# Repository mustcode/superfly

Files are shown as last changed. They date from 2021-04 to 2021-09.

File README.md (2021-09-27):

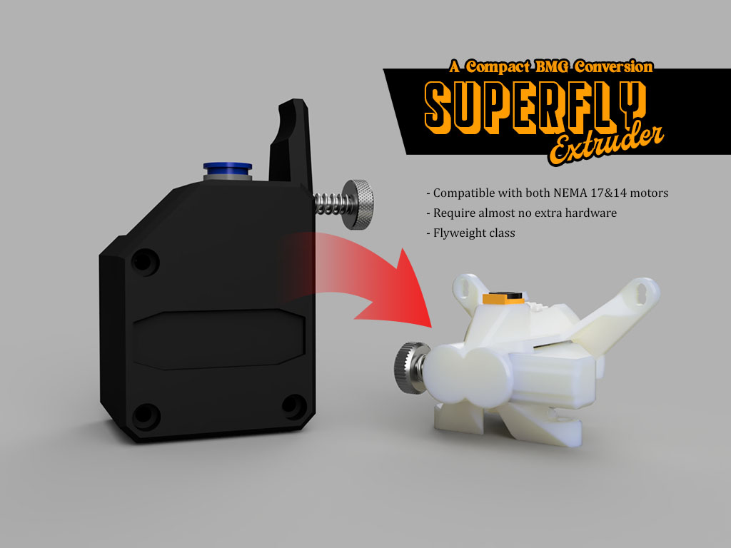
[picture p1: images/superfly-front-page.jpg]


# Superfly Extruder
### A Compact BMG Conversion

** *Update (28th Sep 2021) - A user reported an interference between the tensioner and the plastic gear when used with flexible filaments. This was an error in the design, so it is now corrected. The high-tension version is also removed as the new one should cover all use cases.*

The Superfly is a compact extruder designed to reuse the excellent dual drive gears of the beloved BMG extruder.
As with the BMG, the Superfly is a dual-drive geared extruder with a 3:1 gear ratio. It is designed with the following characteristics in mind:
- compact and lightweight
- short filament path
- balanced center of gravity
- easy to source hardware
- support both NEMA 17 and round NEMA 14 motors
- easy to print

Here are some pictures so that you can get a good idea of what the Superfly looks like:

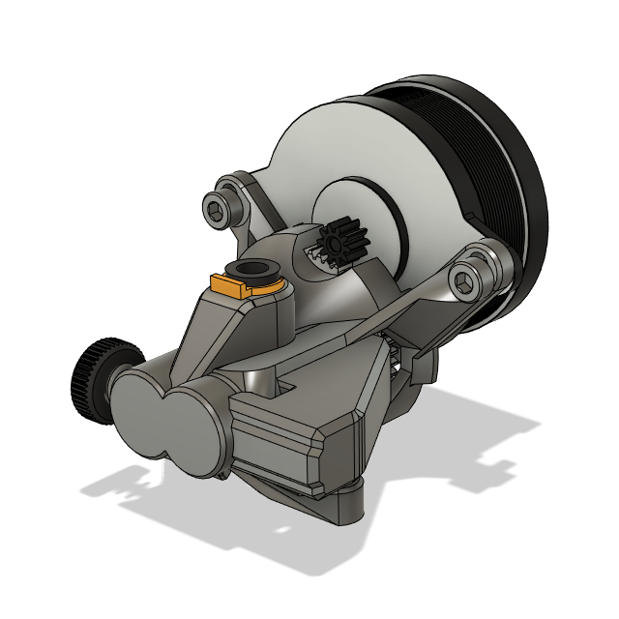
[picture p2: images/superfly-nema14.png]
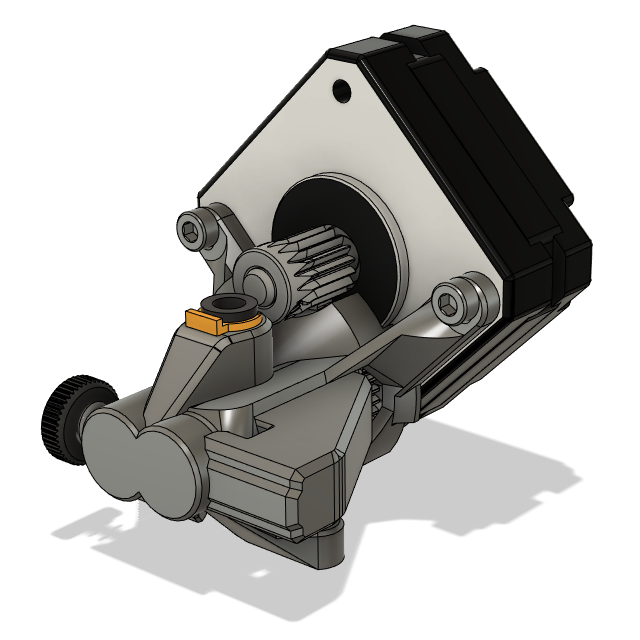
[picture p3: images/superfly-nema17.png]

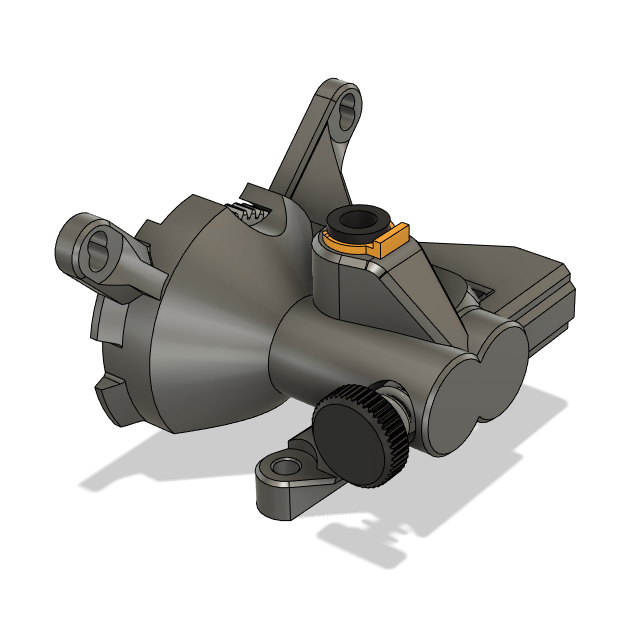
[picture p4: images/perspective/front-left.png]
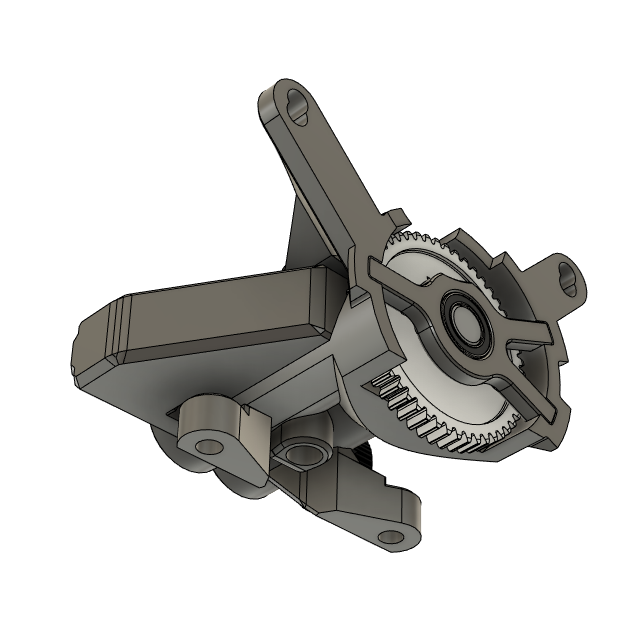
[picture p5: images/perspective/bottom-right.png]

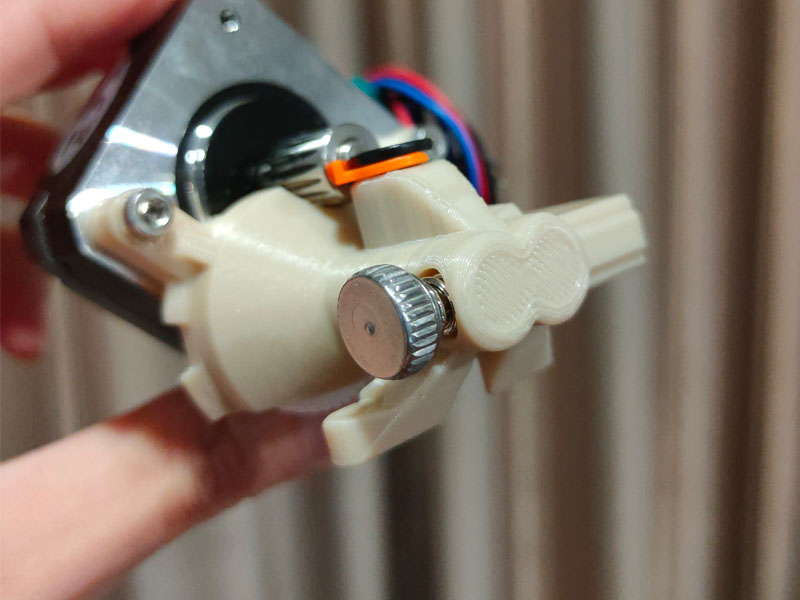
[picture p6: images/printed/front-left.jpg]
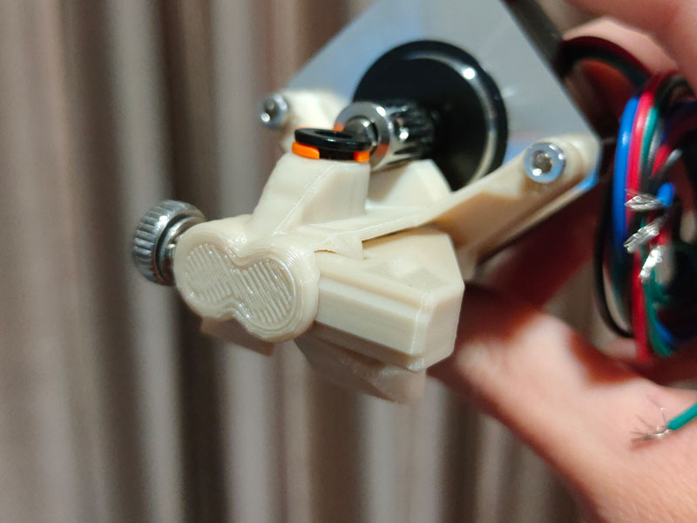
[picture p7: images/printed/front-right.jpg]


The weight of the printed parts for the Superfly comes in at less than 11 gram, a true Flyweight class!
The following shows the weight of a Superfly printed at 0.2mm layer height in PLA+ with 4 walls and plently of infill:

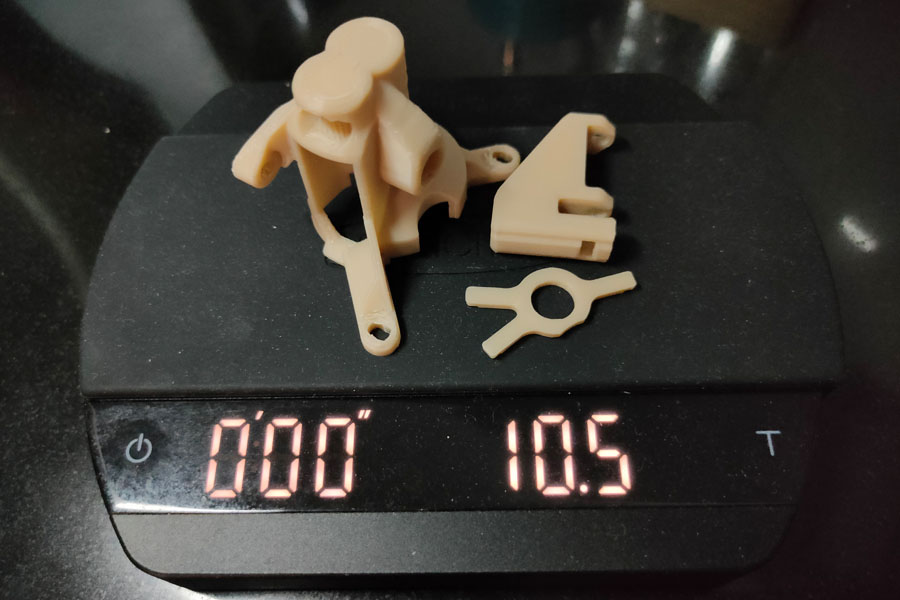
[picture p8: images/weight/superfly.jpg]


For reference, the weight of the printed parts is almost exactly the same as the Sherpa Mini with the same slicer settings:

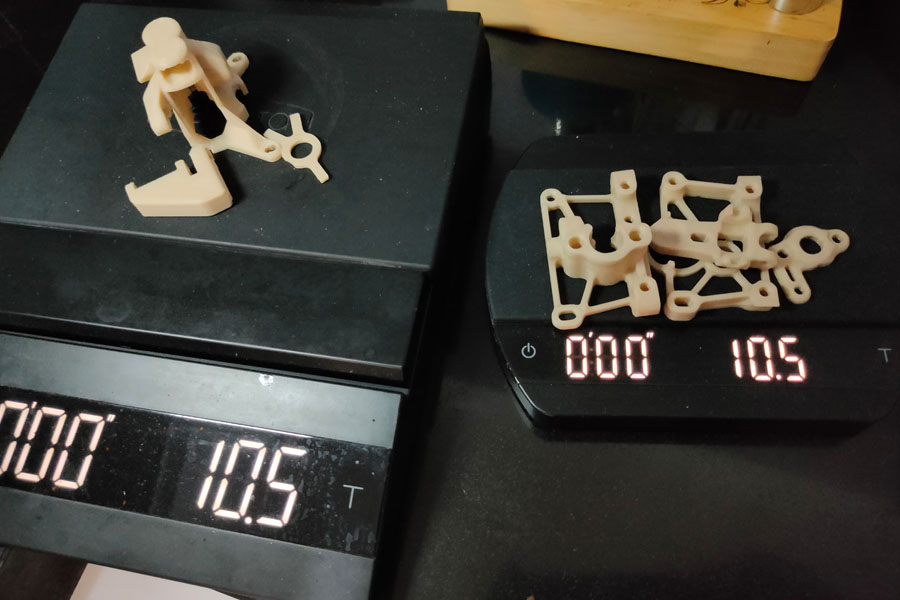
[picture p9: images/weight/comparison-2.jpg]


Fully assembled without motors, the Superfly comes in at around 30-31 gram.

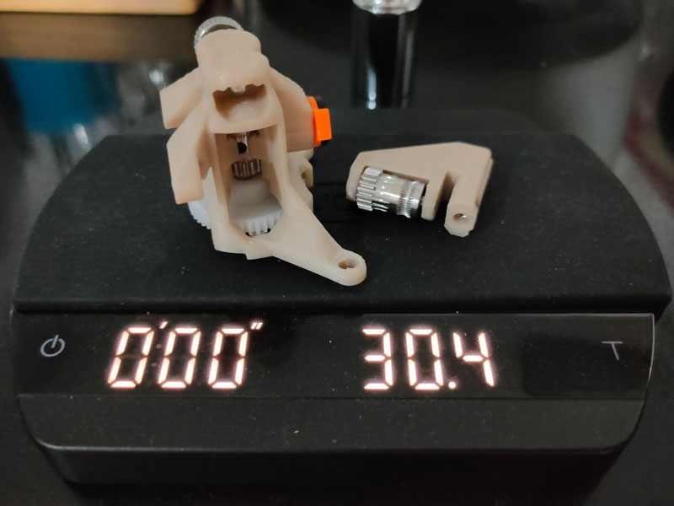
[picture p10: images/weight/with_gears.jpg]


## Parts
You will need the following parts of your BMG:
- the **drive shaft** with the large plastic gear attached
- the **drive gear**, this is the gear that is on the drive shaft
- the **idler gear**, its shaft, and the two needle bearings inside, these are the parts that were on the BMG's tension arm
- **2 x MR85 bearings** that the drive shaft runs on
- **Thumbscrew** and **spring** (the washer is optional)
- the **motor gear**, if you're planning on using a motor without a gear pre-installed

These parts can be removed without any damage to the BMG, so you can reassembled the BMG later on if you wish. If you don't already have a BMG, there are also stores that sell only these internal parts, which should be cheaper than buying a new BMG only to salvage its innards.

In addition to the BMG parts, you will also need the following hardware:
- an M3 nut for securing the thumbscrew
- 4 x M3 screws for mounting (6mm-12mm depending on your motor and mounting needs).

If you're going to be running a reverse-bowden, you'll also need:
- an embedded bowden collet (the type commonly used on a V6 heatsink)
- 4mm OD PTFE tubing

For the motor, as mentioned above, both NEMA 17 and the round NEMA 14 motors are supported. A scalable motor spacer is provided (see **The Motor Spacer** below) to help compensate for the differences in your motor's shaft length, so there's a good chance that you might already have a compatible motor on hand.

## Printed Parts
There are only 4 parts that you need to print:
- The **main housing** holds the drive gear assembly and one of the MR85 bearings.
- The **back housing** holds the other MR85 bearing and keep the drive gear assembly in the main housing.
- The **tensioner** holds the idler gear pressed to the drive gear with the tension from the spring and thumbscrew.
- The **motor spacer**, see details below:

### The Motor Spacer
The motor spacer is an optional part designed to go between the main housing and the motor to allow you to use motors with shaft longer than 15mm. Any longer than 15mm, the shaft can hit the feeding hole where the PTFE tube collet is attached:

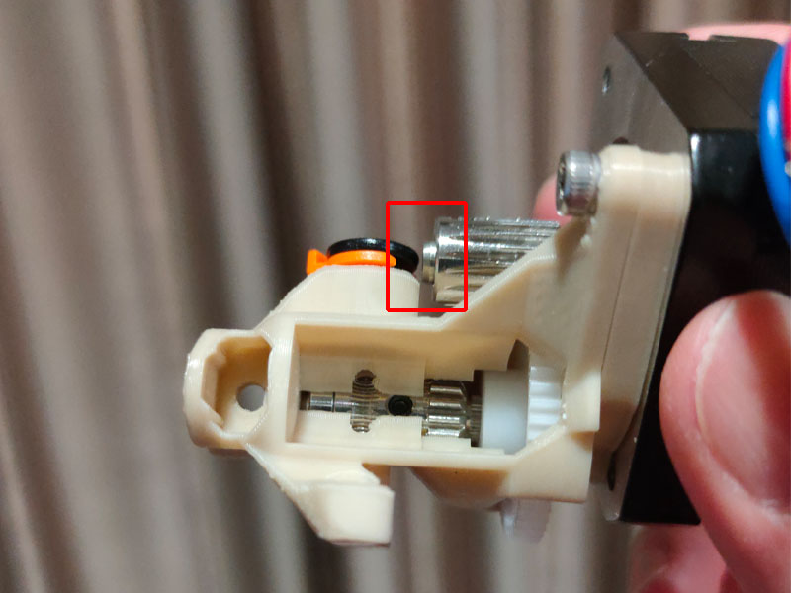
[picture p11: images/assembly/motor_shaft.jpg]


For example, if you're using a motor with 20mm shaft, you will need to scale the provided spacer to the thickness of around 4.5-5mm before printing.
Here's how the extruder looks with and without the spacer:

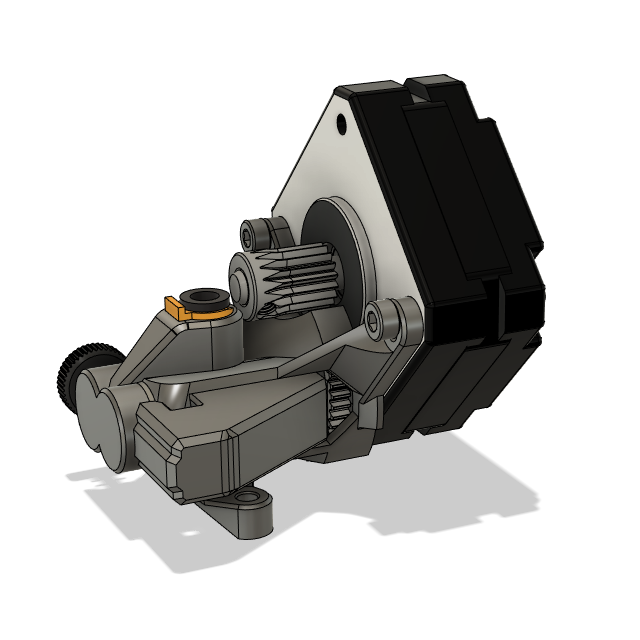
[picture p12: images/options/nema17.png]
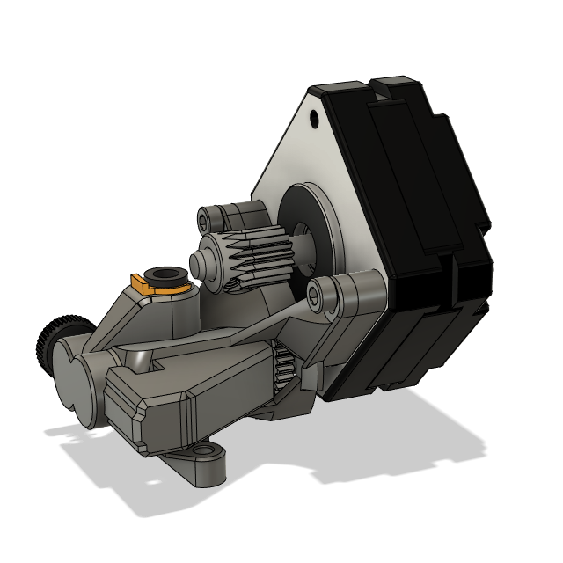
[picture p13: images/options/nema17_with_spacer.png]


Additionally, some variations of the drive shaft are known to be a bit long and may protrude beyond MR85 bearing at the back:

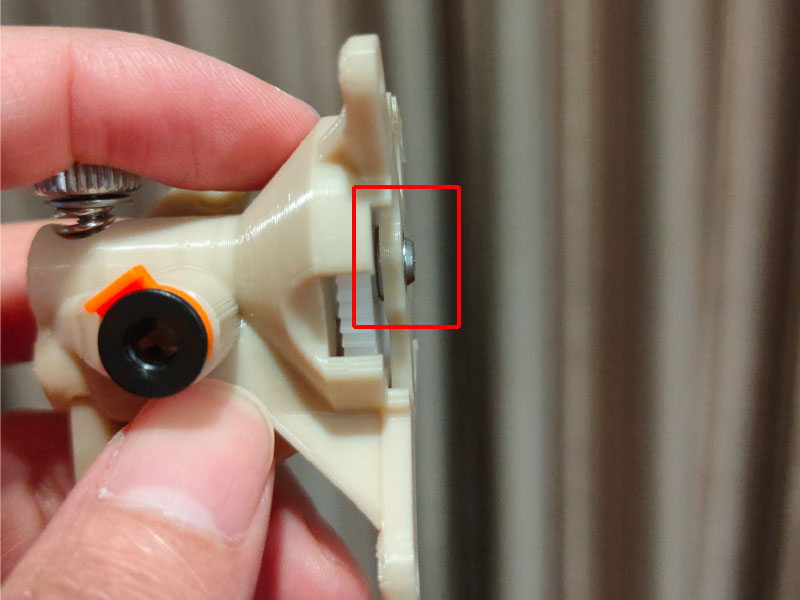
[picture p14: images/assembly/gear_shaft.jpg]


If this is the case for your drive shaft, then you will need a spacer to make sure that the shaft is not pushing against the motor's body. Finally, if you are using a NEMA 14 motor and you prefer to save weight than adding a spacer, you can grind away the protruding portion of the drive shaft, this is commonly done on other similar round NEMA 14 based extruder like the Sherpa Mini. Here's how the extruder should looks with a round NEMA 14 motor:

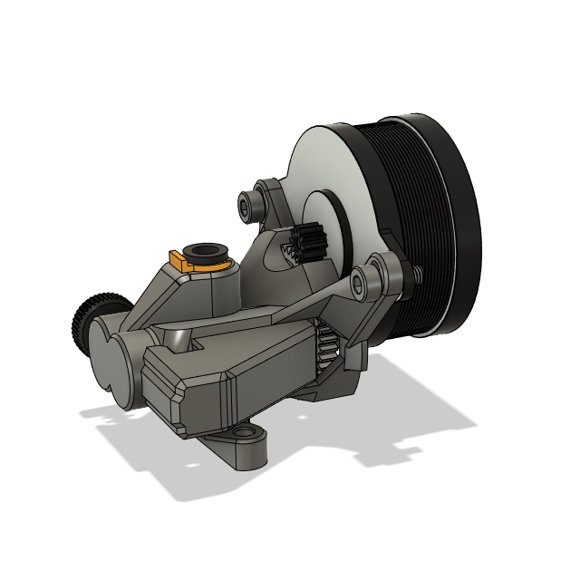
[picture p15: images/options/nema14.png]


## Printing Recommendations:
All parts are printable in under 3 hours and should be an easy print for most modern printers. The following are some recommendations to help increase your chance of success:
- The main housing should be printed "face down" as oriented in the STL, the model is designed to minimize supports in this orientation.
- Supports are only needed for the main housing where the two motor mount holes are. Other overhangs and bridges are very printable.
- Raft should be enabled for the main housing unless you're very confident in your bed-adhesion.
- The tensioner should be printed with plenty of walls and infill to make sure that it doesn't break under stress.
- As with most mechanical prints, your printer should be capable of producing parts with decent dimensional accuracy. If you found that your printed parts are too tight, try the "extra_clearance" version of the main housing instead.

## Post Print:
- Clean up holes with drills
- Check that all parts fit together. Sand if necessary.

## Assembly
Assembly is very straight forward. The following images should be a good enough guide for you to see how all the parts fit together:
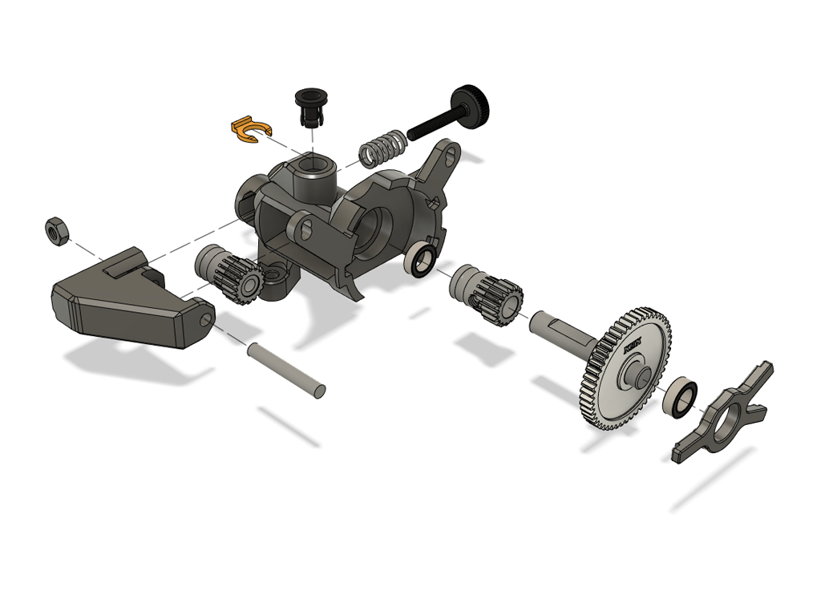
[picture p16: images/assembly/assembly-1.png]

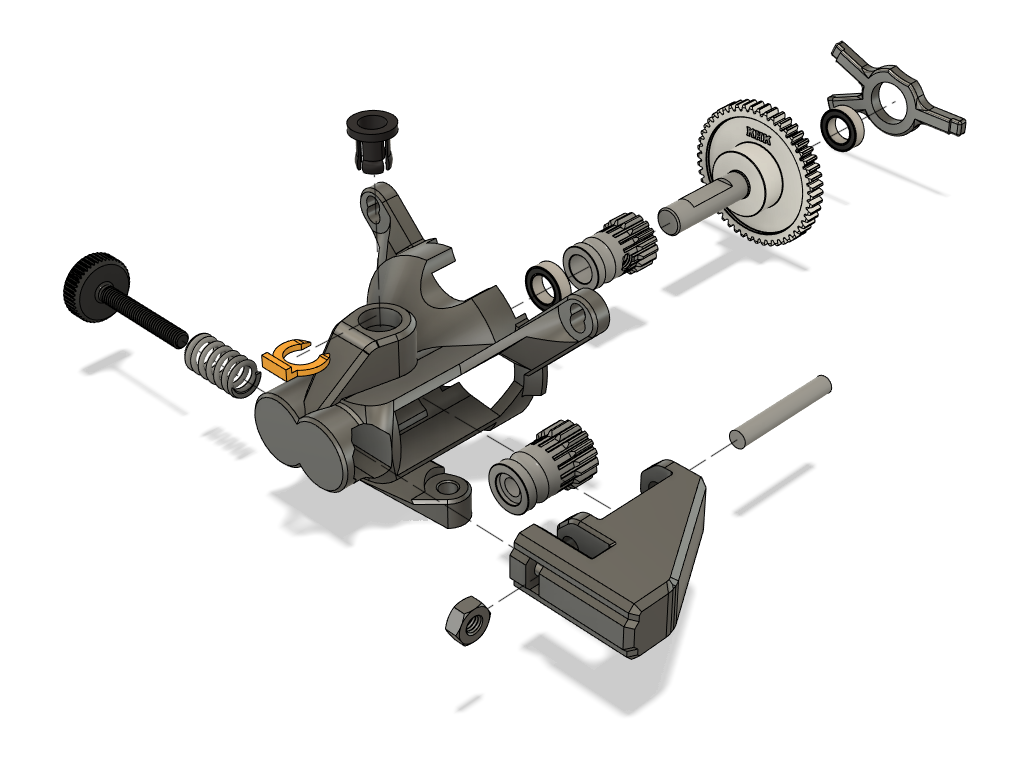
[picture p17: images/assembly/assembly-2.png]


Here is what your main housing should look like before and after assembly:

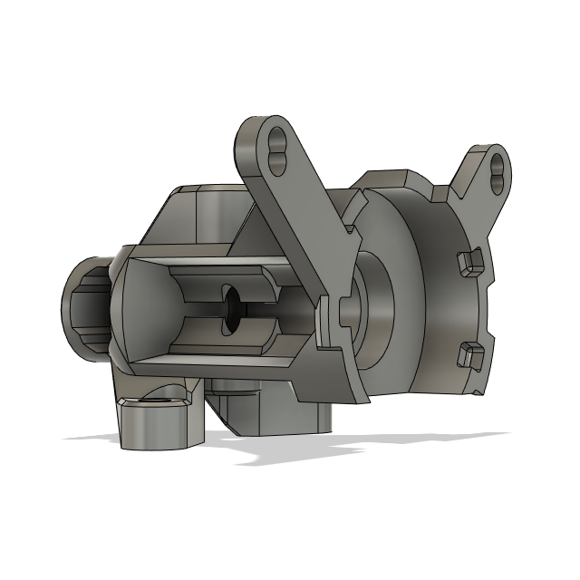
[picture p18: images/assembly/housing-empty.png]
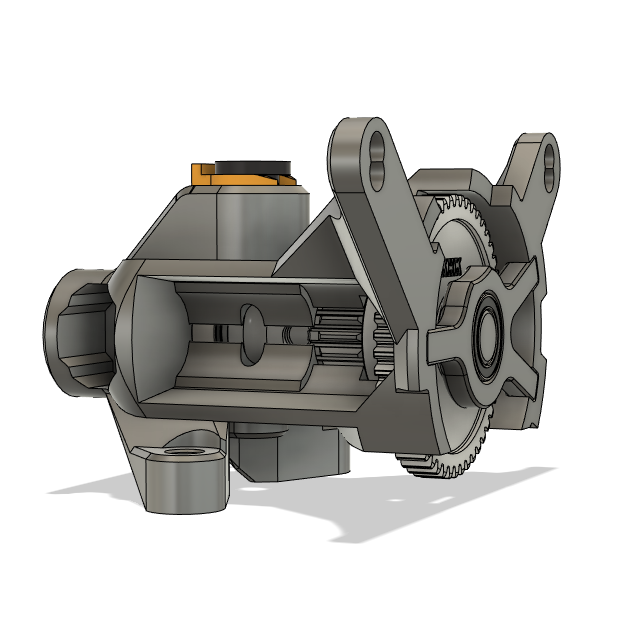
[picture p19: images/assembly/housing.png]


And here is what the tensioner should look like once assembled:

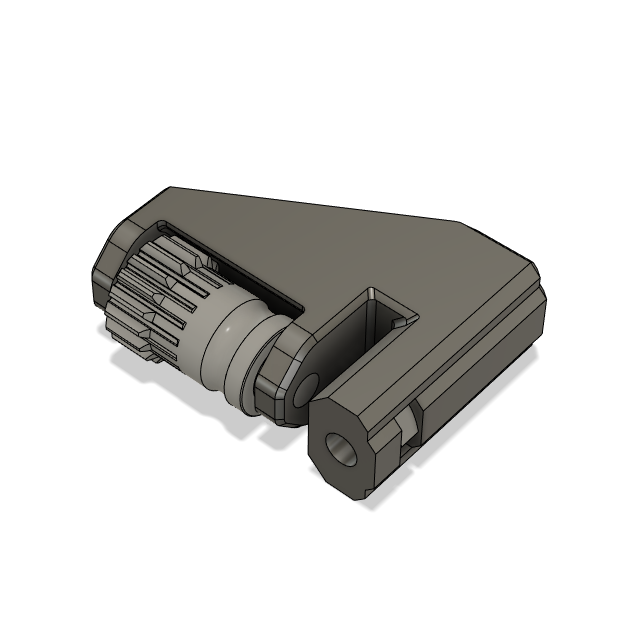
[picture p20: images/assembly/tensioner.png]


One thing to make sure of during assembly is that the drive gear line-up correctly with the filament path. This is best done by inserting a piece of filament as guide before tightening the drive gear fully. Once the drive gear is positioned correctly, when there is a filament moving in the slot, the idler gear will align itself to match the position of the drive gear. This is also true for most extruders with similar dual-drive systems.

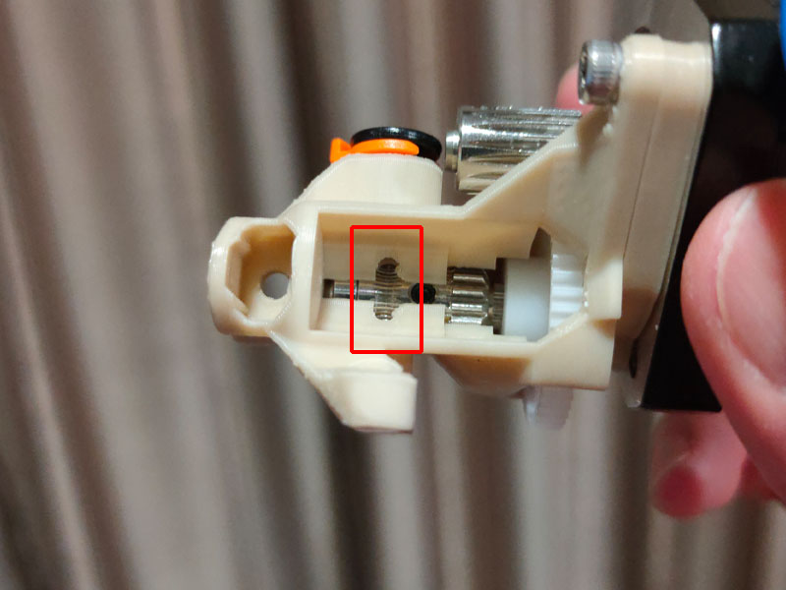
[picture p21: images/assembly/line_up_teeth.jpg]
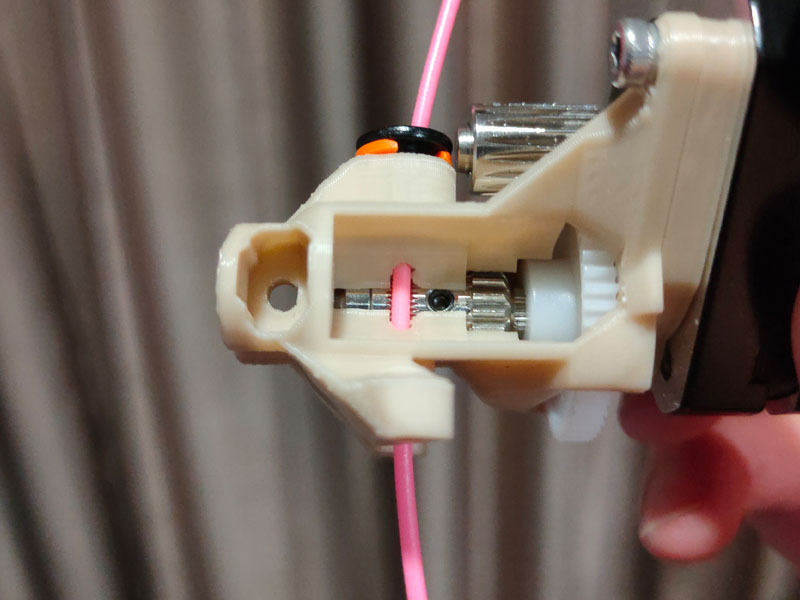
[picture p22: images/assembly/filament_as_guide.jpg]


## Finally,
I'll links to mounts and mods of the Superfly here when I'm informed of them. Hopefully there'll be some makers kind enough to early adopt the Superfly into their home soon :D

That is all! I hope you will enjoy using the Superfly as much as I enjoy creating it :)

Thank you.

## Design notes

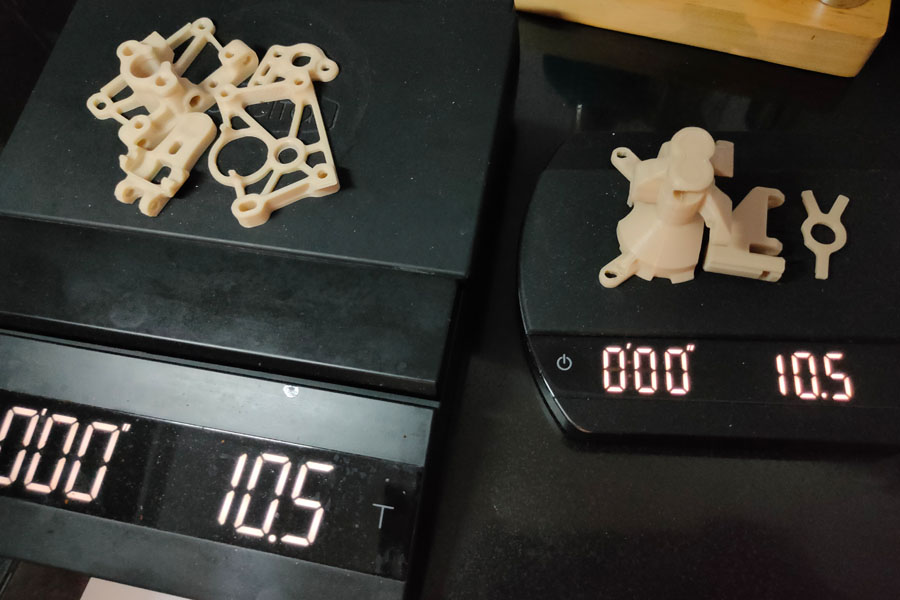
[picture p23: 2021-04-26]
images/weight/comparison-1.jpg

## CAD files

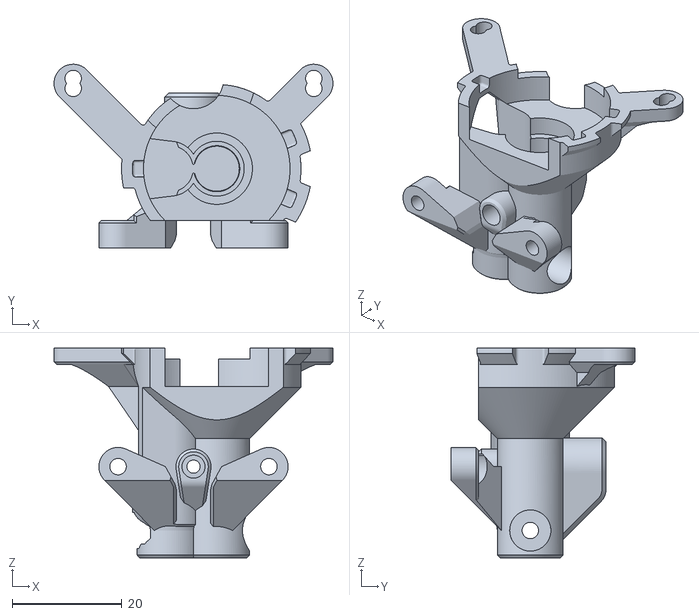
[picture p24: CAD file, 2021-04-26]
main_housing_extra_clearance.stl
50.8 x 33.4 x 38.3

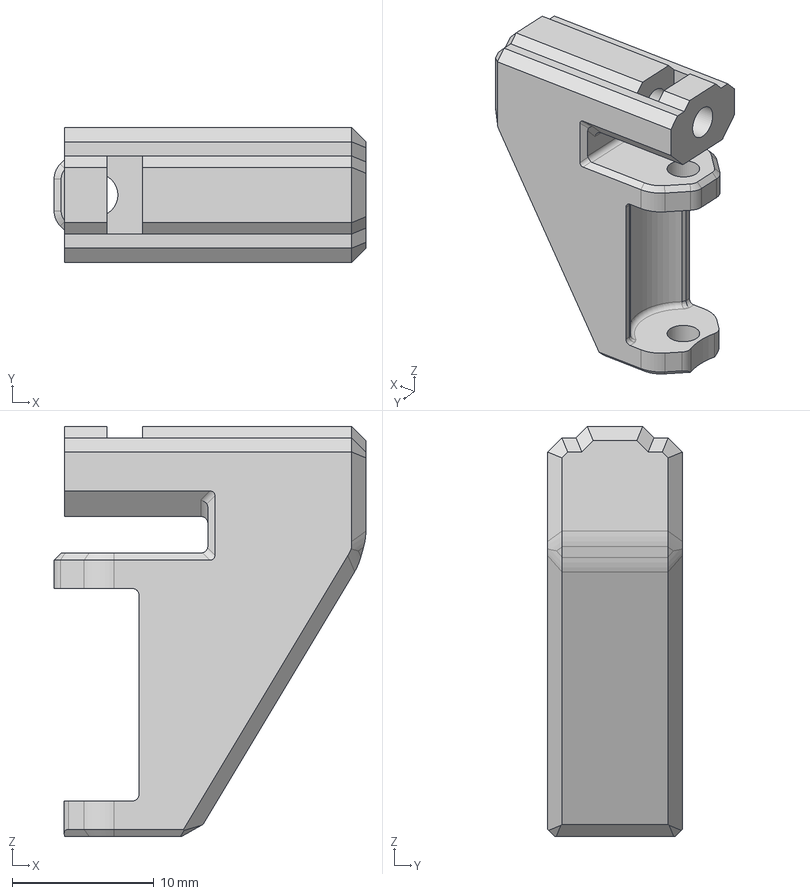
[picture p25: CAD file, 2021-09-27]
tensioner.step
22.0 x 9.50 x 28.9 mm

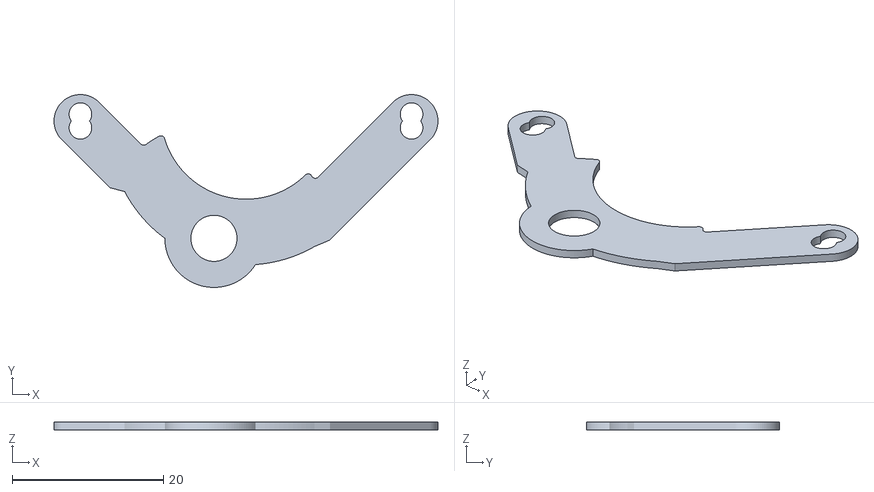
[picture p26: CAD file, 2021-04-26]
motor_spacer_1mm.stl
50.8 x 25.5 x 1.00

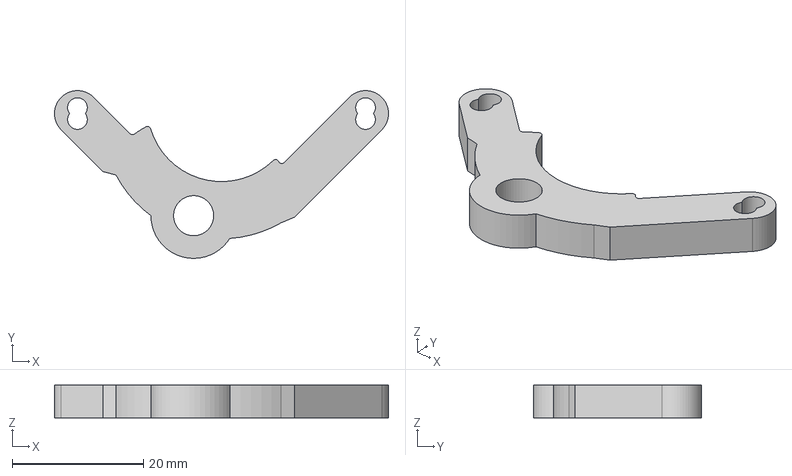
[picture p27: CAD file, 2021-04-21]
motor_spacer_5mm.step
50.8 x 25.5 x 5.00 mm

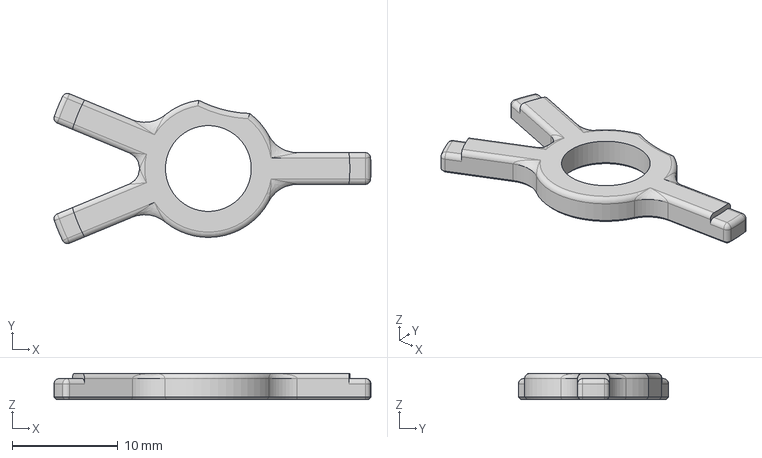
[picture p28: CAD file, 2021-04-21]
back_housing.step
29.9 x 14.2 x 2.50 mm

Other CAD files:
main_housing.step
back_housing.stl
main_housing.stl
motor_spacer_5mm.stl
tensioner.stl

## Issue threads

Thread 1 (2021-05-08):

SuperFly for Deltas

Foxies-CSTL, 2021-05-08:
Hello,
First of all, congratulations for your design!
I have come across your mini-extruder by chance and I am very interested because I have the ideas but not your skills to design this type of object ;-) . Currently I am trying to make tests with a mini-sherpa on a Delta printer assembly but I have an unbalance because the motor is too high. With yours, I will gain height but the best would be to put the motor at the bottom (I have space). I made some rough modifications and printed a draft to see if it goes better (motor at the bottom). If it works mechanically, could you modify the stepper motor attachments as described above?

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

sig. Foxies

mustcode, 2021-05-09:
Nicely done! I'm interested too see how this works out for you, so please do let me know 😄

Foxies-CSTL, 2021-05-15:
Hi,
I finished my tests with your modified extruder. Here is a feedback:
-Assembly is fairly easy, just need a mounting bracket between the extruder and the HotEnd assembly.
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

-My 3D modification is not great because I am not good at modeling ;-) but it works for your tests.
-I had to print the SuperFly body from 101.1% to avoid friction in the assembly.
-The double gear part doesn't work well because it is limited in filament clamping.
-The hole to put the PTFE tube is not long enough (height/depth) to easily remove the tube. The clearance is too small.
-The holes for mounting the stepper motor are too high/double which makes the position of the motor gear slightly off. I re-printed a template without holes to make them after positioning/adjusting the stepper motor.

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

I couldn't print it because I had this problem of the filament drive slipping but with these few modifications, this model is very promising for the Deltas.

Thank you for being able to integrate these modifications that I will test with great interest ;-)
See you later, have a good day .

mustcode, 2021-05-21:
Thank you for the great feedback! I really appreciate them as all the feedback will be what drives the changes in the next iteration.
Also, if you're having issue with filament slipping, try the high-tension version of the tensioner. It was added in after another person reported that the regular tensioner can only hold up to about 80mms, so I made the high version tension which can have a much stronger clamping force.
Also, I noticed that you're not using a Bowden collet, so, I'd recommend using a collet as the hole was designed to fit a collet. It'll help with inserting and removing the PTFE tube.
Cheers!

Foxies-CSTL, 2021-05-21:
Hi,
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

I used bodwen pliers but the gap is not high enough to remove the PTFE without forcing. I also used my tensioner modification. It's better but with my poor inverted motor modification, I have difficulties to get a good grip on the filament. I printed a screen cover in ABS at 80mm/s and I have to watch it because some times it slips (I will put a video). Can you make me a model like mine so I can continue my high speed tests.
Regards,

mustcode, 2021-05-21:
Well, it's not hard to invert, so here it is. But I'm not sure if it'll be any different from yours, so hopefully, this can help you out.
[https://drive.google.com/file/d/1rzZCqRGrUaCEFf2a5QW4L-ouQXXRABdQ/view?usp=sharing](url)

Foxies-CSTL, 2021-05-21:
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
Oh thanks!! Do I have to use FreeCad to transform it into an STL?

Fonsecal, 2021-05-22:
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

Yes , FreeCad  / export / STL

Foxies-CSTL If you can share your suport for the FLSun I will give a try .

Thanks

Foxies-CSTL, 2021-05-24:
> Yes , FreeCad / export / STL
>
> Foxies-CSTL If you can share your suport for the FLSun I will give a try .
Thanks, I had found it ;-)
Here is the support for the SuperFlyDelta.
[QQS_Mount-SuperFly.zip](https://github.com/mustcode/superfly/files/6529223/QQS_Mount-SuperFly.zip)

mustcode, 2021-05-27:
Looks great! I'm glad it worked out :D

Fonsecal, 2021-05-27:
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

Thanks Foxies-CSTL, I have  printed  the support file but is not the complete mount to try on a FLSun QQ s pro . Anyway if possible to share will be great. 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

Closed 2021-06-08.

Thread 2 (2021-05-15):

Full Assembly STEP?

Nickbuddypal, 2021-05-15:
Is there any chance you could provide a fully assembled step file with the hardware? It would be nice to just drag and drop it into place and be able to see where the gears protrude from the design, to help adaptability to other hotends etc.

mustcode, 2021-05-21:
No problems, I'll add the full assembly STEP soon : )

mustcode, 2021-05-21:
Full assembly step added. Enjoy :)

Closed 2021-05-21.

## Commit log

2021-04-21 initial commit. added stls and steps
    [back_housing.step, back_housing.stl, main_housing.step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]
2021-04-26 added a 1mm spacer for easier scaling and main housing with extra clearance
    [main_housing_extra_clearance.stl, motor_spacer_1mm.stl]
2021-05-10 added high-tension tension arm
    [tensioner_high-tension.step, tensioner_high-tension.stl]
2021-05-10 readjust the high-tension arm as the last one was too hard to use.
    [tensioner_high-tension.step, tensioner_high-tension.stl]
2021-05-21 added full-assembly stp
2021-09-27 fixed tensioner interference
    [tensioner.step, tensioner.stl, tensioner_high-tension.step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]
